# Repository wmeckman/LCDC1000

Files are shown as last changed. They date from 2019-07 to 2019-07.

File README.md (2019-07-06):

# LCDC1000
An ESP32 based controller that can drive any kind of LED strip, or motor. Includes microSD, USB-UART, and large voltage range input.

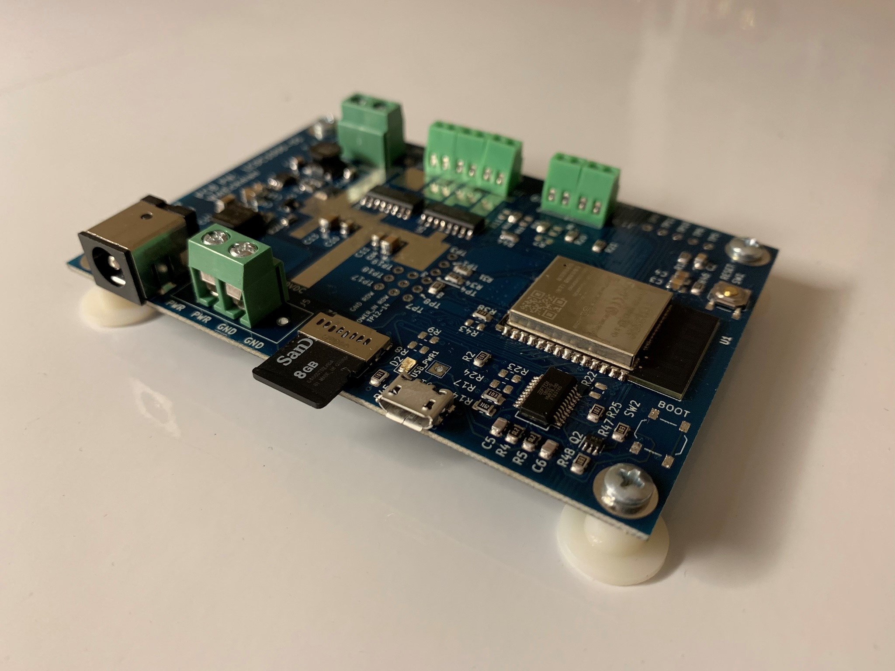
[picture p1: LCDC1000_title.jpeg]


This project started as a Wifi and bluetooth controller that could drive any type of LED strip. LED strip controllers are everywhere, but I wanted a controller that I could customize without using a breadboard. As the project progressed, I wanted this board to be able to drive motors as well. I added a microSD card for file storage, and a USB-UART for debug. Here are the main features:

ESP32 based using MicroPython
Drives Any type of LED strip - RGB, RGBW, WS2812, APA102, Neopixel, etc
Wide input power range: 4.5V to 30V DC.
Input power via Barrel Jack 2.10mm ID (0.083"), 5.50mm OD or Terminal Block.
Reverse polarity input power protection.
Drives 1 stepper motor in full H-bridge configuration.
Drives 2 bipolar DC motors in half H-bridge configuration.
Drives 4 Unipolar DC Motors.
Additional outputs for servo motors available.
Current sense for motor/LED drivers.
Outputs on terminal blocks.

Power: 4.5V-30V DC power can be applied either through the barrel jack or the terminal block (not both). An on-board regulator is used to create the 3.3V necessary for the ESP32, MicroUSB, and USB-UART.  The power input on J6 and J5 is equal to the power output on J7.  Use a power supply that is designed to drive what is connected on the output.  For example, if driving a 12V RGB LED strip, use a 12V power supply.  

To use the board, connect whatever you're controlling (LED, motor, etc) to the terminal blocks (J3, J4, J7), then apply power to J5 or J6.  The 'connection notes' section provides more in depth instruction by device.

Pinouts

J6 Barrel Jack Input Power

    Pin:  +Vin 4.5V to 30V
    Shield:  Ground

J5 Input Power Terminal Block

    1:  +Vin 4.5V to 30V
    2:  +Vin 4.5V to 30V
    3:  Ground
    4:  Ground

J7 Output Power Terminal Block

    1:  +Vout
    2:  +Vout
    3:  Ground
    4:  Ground

J3, J4, J8 High Current Motor and RGB, RGBW LED Drive Terminal Block

    J3-1:  Power Out
    J3-8:  Drive1Out1
    J4-1:  Drive1Out2
    J4-2:  Drive2Out1
    J8-1:  Drive2Out2
    J8-2:  Ground

J9 and J10:  SPI, and PWM Drive Signals for Servo Motor, individually addressable LED's Terminal Block

    J9-1:  GPIO_2 (ESP32 IO2)
    J9-2:  GPIO_5 (ESP32 IO5) 
    J10-1:  LED_DATA (ESP IO19)
    J10-2:  LED_CLK (ESP IO18)

Test Point Header Pins

    TP1:  TDI_SD_MISO - Primarily used to SD card, but can be used for JTAG
    TP2:  TDO_SD_CD - Primarily used to SD card, but can be used for JTAG
    TP3:  TMS_SD_CLK - Primarily used to SD card, but can be used for JTAG
    TP4:  TCK_SD_MOSI - Primarily used to SD card, but can be used for JTAG
    TP5:  ESP32 Enable
    TP7:  IO17
    TP8:  GPIO_0 - ESP32 IO0
    TP9:  ESP32 IO35
    TP10:  ESP32 SENSOR_VP
    TP11:  ESP32 SENSOR_VN
    TP12:  +Vout
    TP13:  +Vout
    TP14:  +Vout
    TP17:  GND
    TP18:  GND
    TP19:  GND
    USBPWR_TP:  USB Power 

Note:  TP2, TP7, TP8 are arranged on the PCB with TP12-TP14, and TP17-TP19 to be compatible with servo motor connections.

---------------------------------------------------------------------------------------------------

Connection Notes:  Overview of connections for various devices

Individually addressable LED's - WS2812, NeoPixel, etc.

    J7-1:  LED Power
    J7-4:  LED Ground
    J9-1:  LED Data

Individually Addressable LED's - APA102, SK9822, DotStar, etc.

    J7-1:  LED Power
    J7-4:  LED Ground
    J10-1:  LED Data
    J10-2:  LED Clock

J10-1, and J10-2 are connected to the ESP32 SPI bus.  This provides the highest speed possible.  Additional LED strips can be connected using lower speed GPIO pins.  

Low speed GPIO connection example:

    J7-2:  LED Power
    J7-3:  LED Ground
    J9-1:  LED Data
    J9-2:  LED Clock

RGB Strips

    J7-1: LED Power
    J3-1: R
    J3-2: G
    J3-3: B

RGBW Strips

    J3-1: LED Power
    J3-2: R
    J4-1: G
    J4-2: B
    J8-1: W

Bipolar DC Stepper Motor

    J3-2:  Coil1+
    J4-1:  Coil1-
    J4-2:  Coil2+
    J8-1:  Coil2-

Unipolar DC Stepper Motor 5 Wire

    J3-2:  Coil 1
    J4-1:  Coil 2
    J4-2:  Coil 3
    J8-1:  Coil 4
    J7-3:  Ground

Unipolar DC Stepper Motor 6 Wire

    J3-2:  Coil 1
    J4-1:  Coil 2
    J4-2:  Coil 3
    J8-1:  Coil 4
    J7-3:  Ground
    J7-4:  Ground

DC Motor Unidirectional  :  Connect up to 4

    Use J3-2 or J4-1 or J4-2 or J8-1 for (+) wire
    Use J7-3 or J7-4 for (-) wire

DC Bidirectional Motor  :  Connect up to 2

    J3-2: Motor 1 (+) 
    J4-1: Motor 1 (-)
    J4-2: Motor 2 (+) 
    J8-1: Motor 2 (-)

Servo Motors

    J7-1 Servo 1 Power +
    J7-3 Servo 1 Power -
    J9-1 Servo 1 Control

    J7-2 Servo 2 Power +
    J7-4 Servo 2 Power -
    J9-2 Servo 2 Control

Additional Servos can be connected on the header pins.

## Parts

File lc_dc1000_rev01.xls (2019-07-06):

Reference | Quantity | Value | MFR | MFR#
C12 C9 C13 C14 | 4 | 4.7uF | Samsung | CL31B475KBHNNNE
C15 | 1 | 1uF | Samsung | CL21B105KPFNNNE
C18 C4 | 2 | 10uF | Samsung | CL21A106KQCLRNC
C3 C2 C1 C10 C11 C16 | 6 | 0.1uF | Samsung | CL21F104ZBCNNNC
C6 C5 | 2 | 27pF | Samsung | CL21C270JBANNNC
D1 | 1 | 4.3V | OnSemi | BZX84C4V3LT1G
D2 | 1 | LED | Lite-On | LTST-C171GKT
J1 | 1 | 10118193-0001LF | Amphenol | 10118193-0001LF
J2 | 1 | Micro_SD_Card | Molex | 1051620001
J3 J4 J8 J10 J9 | 0 | Screw_Terminal_01x02 | E-Simpo | ELT128-2.54-2P
J6 | 0 | Barrel_Jack | CUI | PJ-063AH
J7 J5 | 0 | Screw_Terminal_01x04 | Wurth | 691137710004
L1 | 1 | 15uH | Taiyo Yuden | NR6045T150M
Q1 | 1 | AOD4189 | Alpha & Omega | AOD4189
Q2 | 1 | MBT3904DW1 | On Semi | MBT3904DW1T1G
R20 R21 R19 R18 | 4 | 10 | Bourns | CR0805-JW-100ELF
R27 R28 R39 R41 R29 R30 R42 R44 R25 R46 | 10 | 1k | Bourns | CR0805-JW-102ELF
R31 R32 R33 R34 R45 | 5 | 100 | Bourns | CR0805-JW-101ELF
R35 R26 R14 | 3 | 31.6k | Rohm | MCR10ERTF3162
R36 R1 R3 R2 R37 R38 R17 R12 R48 R47 | 10 | 10k | Bourns | CR0805-JW-103ELF
R4 R5 | 2 | 27 | StackPole | RMCF0805JT27R0
SW1 | 1 | SW_Push | Uxcell | a12011500ux0296
U1 | 1 | ESP32-WROOM-32D | Espressif | ESP32-WROOM-32D
U2 | 1 | FT231XS | FTDI | FT231XS-R
U3 | 1 | MCP16311MS | Microchip | MCP16311T-E/MS
U4 U5 | 2 | VNH7100ASTR | ST | VNH7100ASTR
 | 62

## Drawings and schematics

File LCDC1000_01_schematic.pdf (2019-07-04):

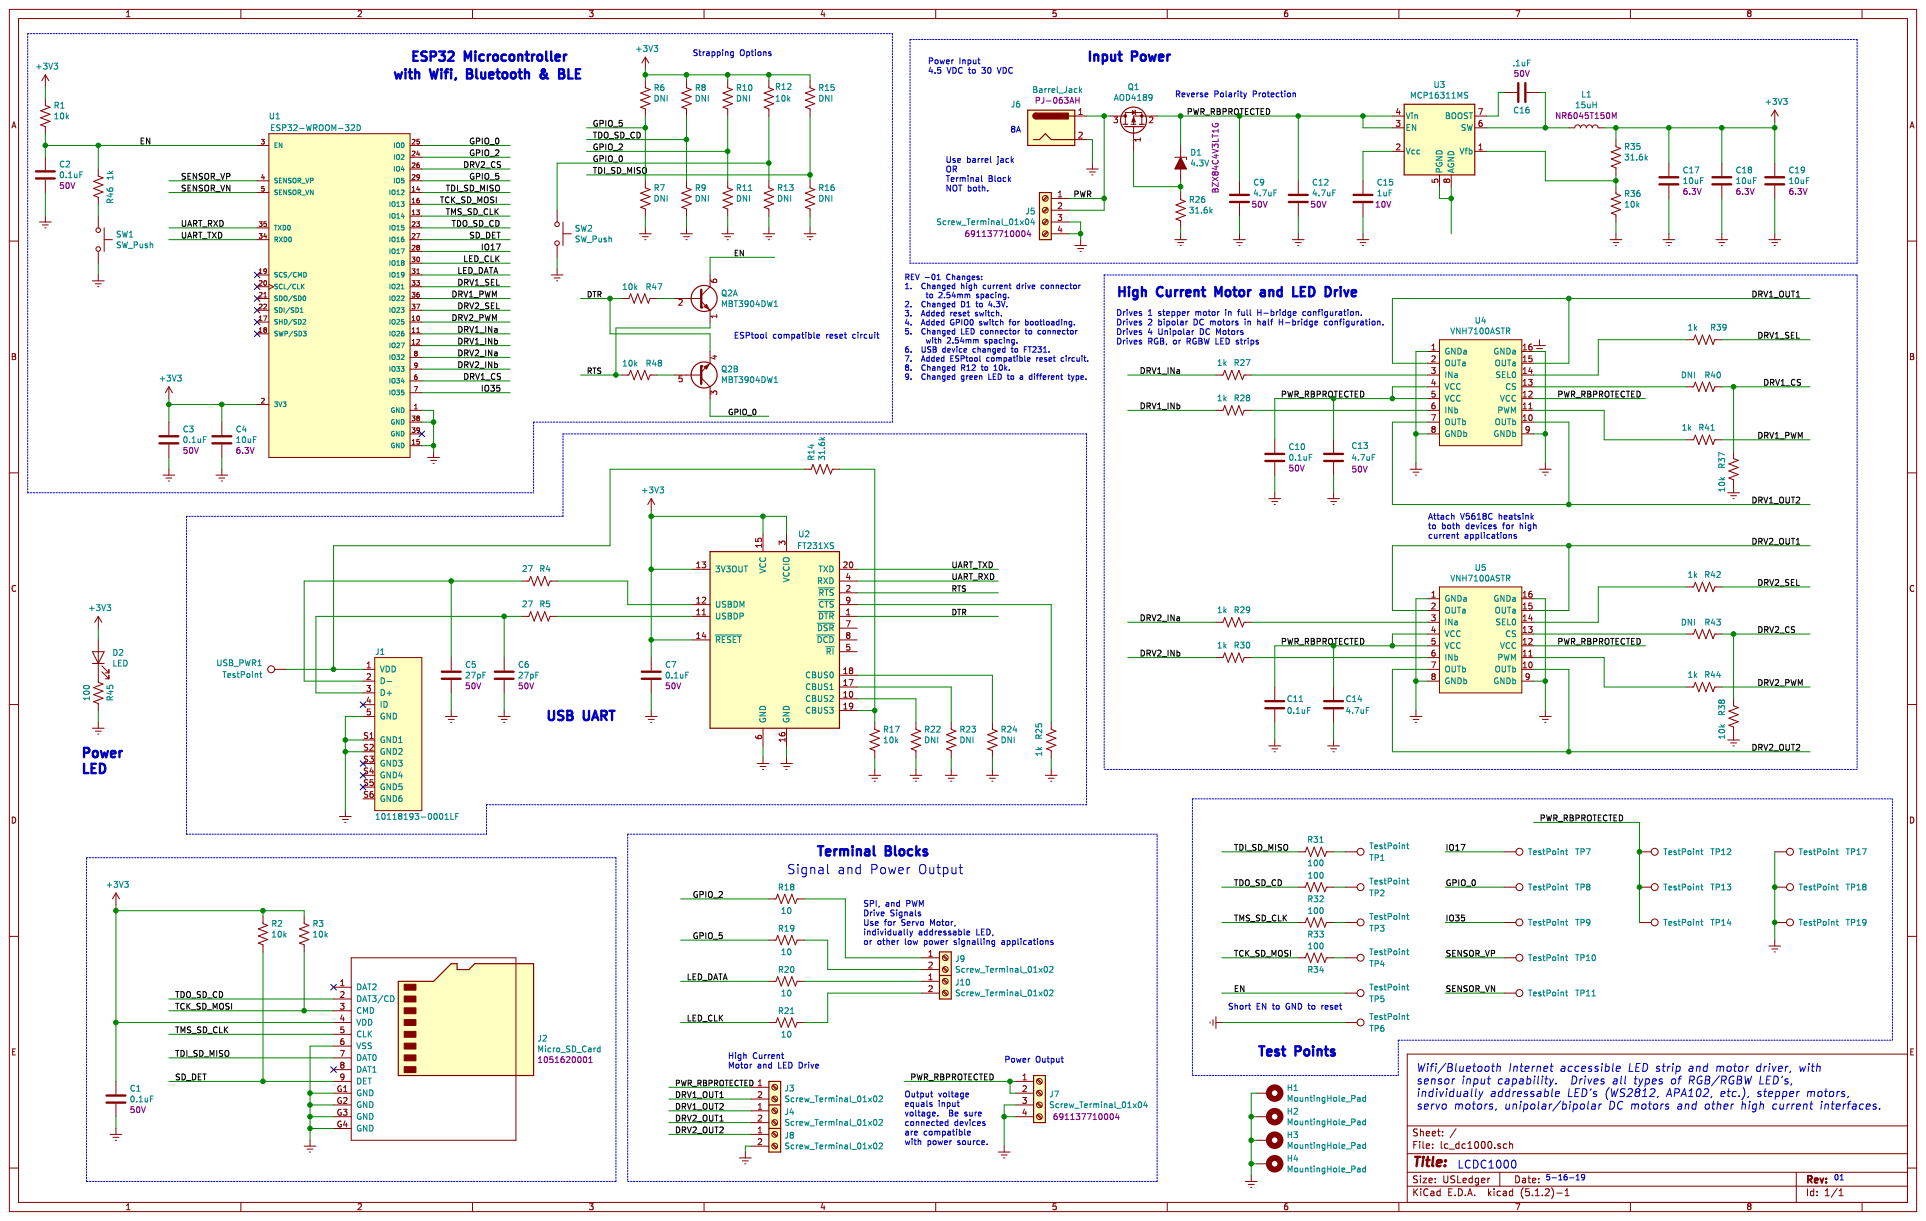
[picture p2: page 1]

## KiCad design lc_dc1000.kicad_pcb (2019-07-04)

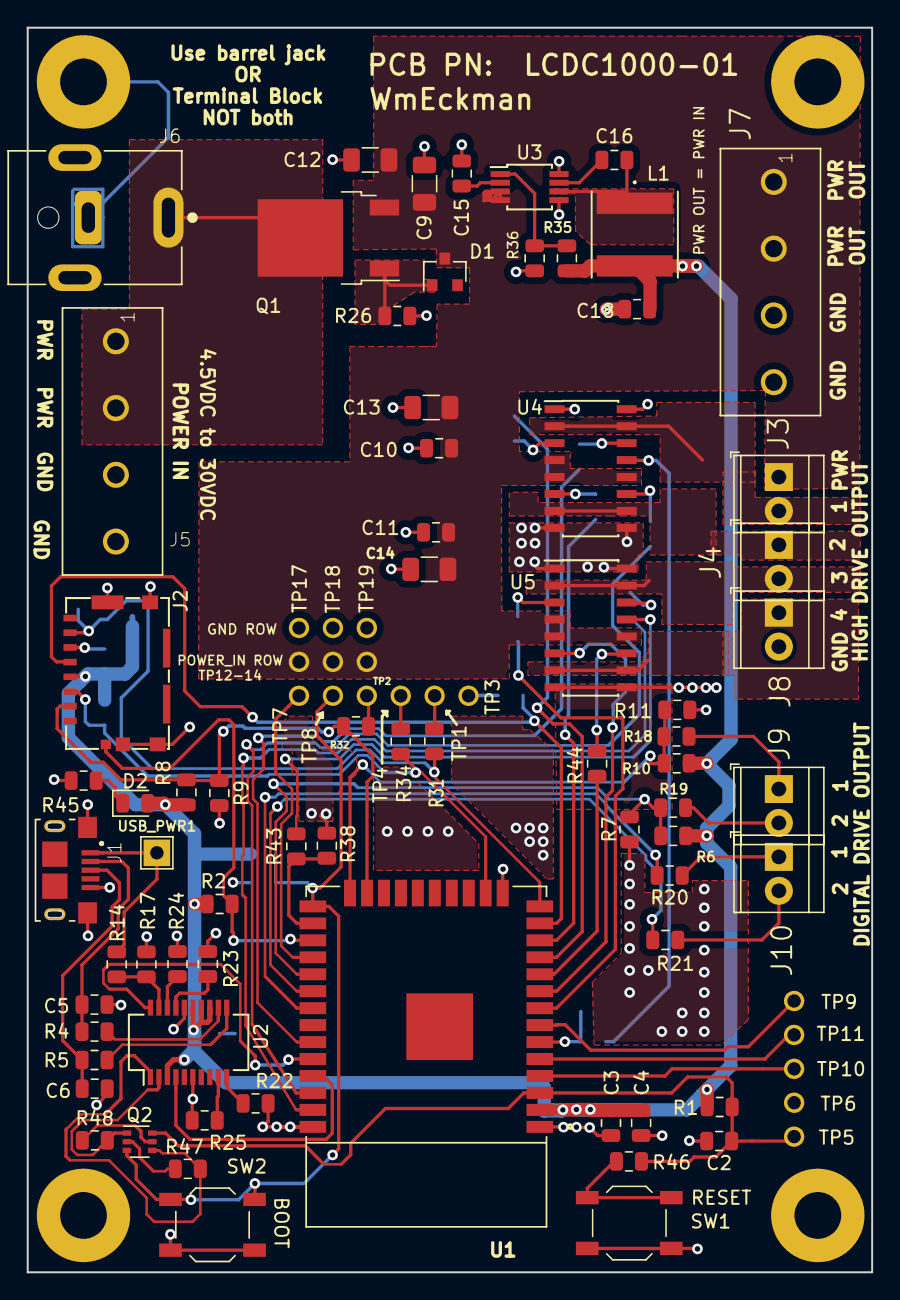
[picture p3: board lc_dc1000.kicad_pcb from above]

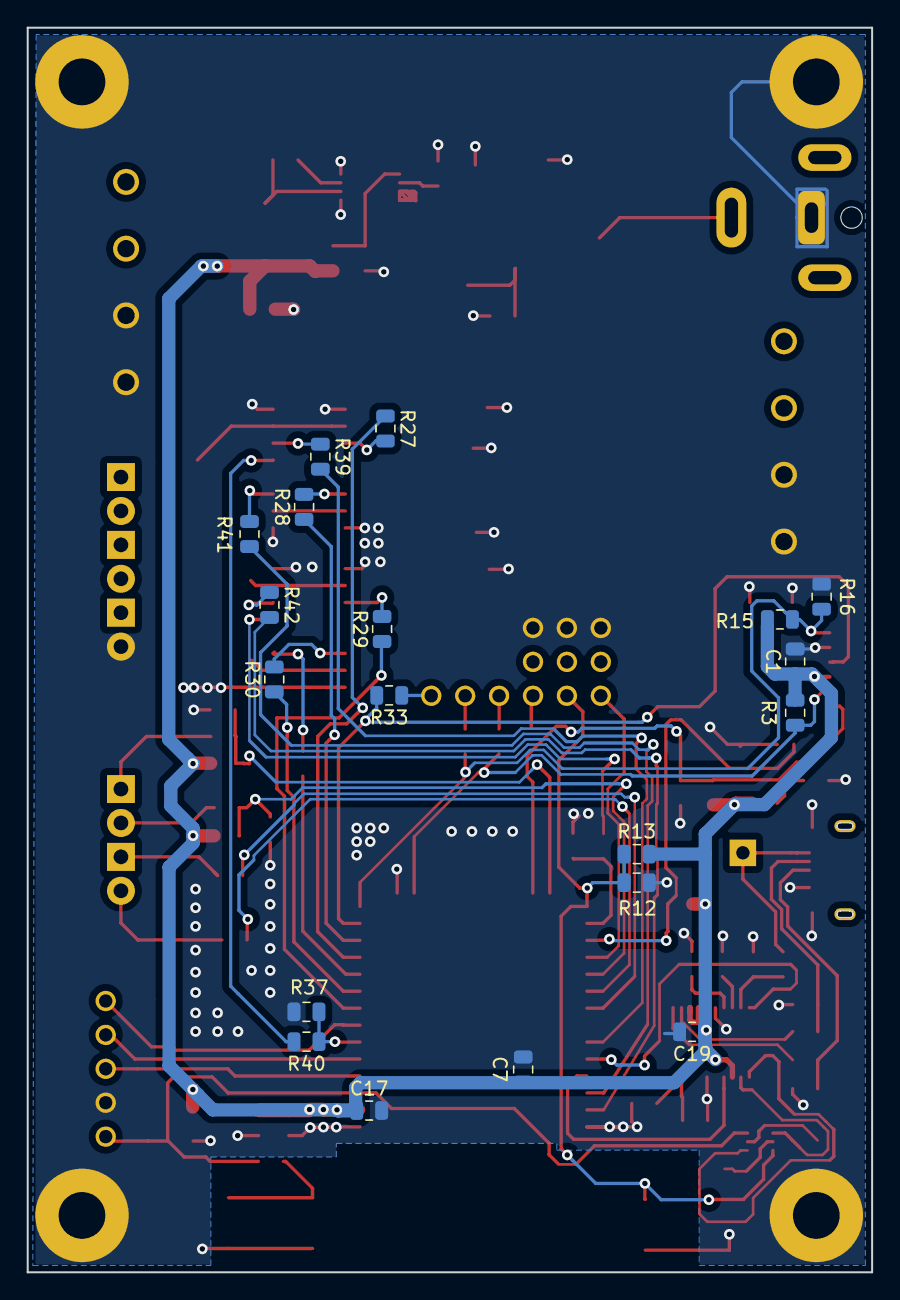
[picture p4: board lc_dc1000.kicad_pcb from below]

Board: 2 copper layers, 63.2 x 93.2 mm, 110 parts (19 on the bottom side), 74 nets.

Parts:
C1, C2, C3, C7, C10, C11: 0.1uF; C_0805_2012Metric
C4, C17, C18, C19: 10uF; C_0805_2012Metric
C5, C6: 27pF; C_0805_2012Metric
C9, C12, C13, C14: 4.7uF; C_1206_3216Metric
C15: 1uF; C_0805_2012Metric
C16: .1uF; C_0805_2012Metric
D1: 4.3V; D_SOT-23_ANK
D2: LED; LED_0805_2012Metric
H1, H2, H3, H4: MountingHole_Pad; MountingHole_3.5mm_Pad
J1: 10118193-0001LF; usb
J2: Micro_SD_Card; 1051620001_microsd
J3, J4, J8, J9, J10: Screw_Terminal_01x02; TerminalBlock_TE_282834-2_1x02_P2.54mm_Horizontal
J5, J7: Screw_Terminal_01x04; 691137710004
J6: Barrel_Jack; CUI_PJ-063AH
L1: 15uH; NR6045T150M
Q1: AOD4189; TO-252-2_AOD4189
Q2: MBT3904DW1; SOT-363_SC-70-6
R1, R2, R3, R12, R17, R36, R37, R38, R47, R48: 10k; R_0805_2012Metric
R4, R5: 27; R_0805_2012Metric
R6, R7, R8, R9, R10, R11, R13, R15, R16, R22, R23, R24, R40, R43: DNI; R_0805_2012Metric
R14, R26, R35: 31.6k; R_0805_2012Metric
R18, R19, R20, R21: 10; R_0805_2012Metric
R25, R27, R28, R29, R30, R39, R41, R42, R44, R46: 1k; R_0805_2012Metric
R31, R32, R33, R34, R45: 100; R_0805_2012Metric
SW1, SW2: SW_Push; SW_SPST_TL3342
TP1, TP2, TP3, TP4, TP5, TP6, TP7, TP8, TP9, TP10, TP11, TP12, TP13, TP14, TP17, TP18, TP19: TestPoint; 1mm_tp
U1: ESP32-WROOM-32D; MODULE_ESP32-WROOM-32D
U2: FT231XS; SSOP-20_3.9x8.7mm_P0.635mm
U3: MCP16311MS; MSOP-8_3x3mm_P0.65mm
U4, U5: VNH7100ASTR; SOIC-16_3.9x9.9mm_P1.27mm
USB_PWR1: TestPoint; TestPoint_THTPad_2.0x2.0mm_Drill1.0mm

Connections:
+3V3: C1.1, C3.1, C4.1, C7.1, C17.1, C18.1, C19.1, D2.2, J2.4, L1.2, R1.1, R2.1, R3.1, R6.1, R8.1, R10.1, R12.1, R15.1, R35.1, U1.2, U2.3, U2.13, U2.14, U2.15
/DRV1_CS: R37.1, R40.1, U1.6
/DRV1_INa: R27.1, U1.11
/DRV1_INb: R28.1, U1.12
/DRV1_OUT1: J3.2, U4.2, U4.15
/DRV1_OUT2: J4.1, U4.7, U4.10
/DRV1_PWM: R41.2, U1.36
/DRV1_SEL: R39.2, U1.33
/DRV2_CS: R38.1, R43.1, U1.26
/DRV2_INa: R29.1, U1.8
/DRV2_INb: R30.1, U1.9
/DRV2_OUT1: J4.2, U5.2, U5.15
/DRV2_OUT2: J8.1, U5.7, U5.10
/DRV2_PWM: R44.2, U1.10
/DRV2_SEL: R42.2, U1.37
/DTR: Q2.4, R47.2, U2.1
/EN: C2.1, Q2.6, R1.2, R46.1, TP5.1, U1.3
/GPIO_0: Q2.3, R12.2, R13.1, SW2.1, TP8.1, U1.25
/GPIO_2: R10.2, R11.1, R18.2, U1.24
/GPIO_5: R6.2, R7.1, R19.2, U1.29
/IO17: TP7.1, U1.28
/IO35: TP9.1, U1.7
/LED_CLK: R21.2, U1.30
/LED_DATA: R20.2, U1.31
/PWR: J5.1, J5.2, J6.1, Q1.3
/PWR_RBPROTECTED: C9.1, C10.1, C11.1, C12.1, C13.1, C14.1, D1.1, J3.1, J7.1, J7.2, Q1.2, TP12.1, TP13.1, TP14.1, U3.3, U3.4, U4.4, U4.5, U4.12, U5.4, U5.5, U5.12
/RTS: Q2.1, R48.2, U2.2
/SD_DET: J2.9, R2.2, U1.27
/SENSOR_VN: TP11.1, U1.5
/SENSOR_VP: TP10.1, U1.4
/TCK_SD_MOSI: J2.3, R3.2, R34.2, U1.16
/TDI_SD_MISO: J2.7, R15.2, R16.1, R31.1, U1.14
/TDO_SD_CD: J2.2, R8.2, R9.1, R32.2, U1.23
/TMS_SD_CLK: J2.5, R33.2, U1.13
/UART_RXD: U1.35, U2.4
/UART_TXD: U1.34, U2.20
Earth: C1.2, C2.2, C3.2, C4.2, C5.2, C6.2, C7.2, C9.2, C10.2, C11.2, C12.2, C13.2, C14.2, C15.2, C17.2, C18.2, C19.2, H1.1, H2.1, H3.1, H4.1, J1.5, J1.S1, J1.S2, J2.6, J2.G1, J2.G2, J2.G3, J2.G4, J5.3, J5.4, J6.2, J7.3, J7.4, J8.2, R7.2, R9.2, R11.2, R13.2, R16.2, R17.2, R22.2, R23.2, R24.2, R25.1, R26.2, R36.2, R37.2, R38.2, R45.2, SW1.2, SW2.2, TP6.1, TP17.1, TP18.1, TP19.1, U1.1, U1.15, U1.38, U2.6, U2.16, U3.5, U3.8, U4.1, U4.8, U4.9, U4.16, U5.1, U5.8, U5.9, U5.16
unnamed: C5.1, J1.2, R4.1
unnamed: C6.1, J1.3, R5.1
unnamed: C15.1, U3.2
unnamed: C16.1, L1.1, U3.6
unnamed: C16.2, U3.7
unnamed: D1.2, Q1.1, R26.1
unnamed: D2.1, R45.1
unnamed: J1.1, R14.1, USB_PWR1.1
unnamed: J9.1, R18.1
unnamed: J9.2, R19.1
unnamed: J10.1, R20.1
unnamed: J10.2, R21.1
unnamed: Q2.2, R47.1
unnamed: Q2.5, R48.1
unnamed: R4.2, U2.12
unnamed: R5.2, U2.11
unnamed: R14.2, R17.1, U2.19
unnamed: R22.1, U2.10
unnamed: R23.1, U2.17
unnamed: R24.1, U2.18
unnamed: R25.2, U2.9
unnamed: R27.2, U4.3
unnamed: R28.2, U4.6
unnamed: R29.2, U5.3
unnamed: R30.2, U5.6
unnamed: R31.2, TP1.1
unnamed: R32.1, TP2.1
unnamed: R33.1, TP3.1
unnamed: R34.1, TP4.1
unnamed: R35.2, R36.1, U3.1
unnamed: R39.1, U4.14
unnamed: R40.2, U4.13
unnamed: R41.1, U4.11
unnamed: R42.1, U5.14
unnamed: R43.2, U5.13
unnamed: R44.1, U5.11
unnamed: R46.2, SW1.1

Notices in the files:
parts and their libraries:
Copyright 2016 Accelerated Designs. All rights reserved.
